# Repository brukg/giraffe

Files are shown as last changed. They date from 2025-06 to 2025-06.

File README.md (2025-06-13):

<!-- @format -->

# _giraffe: a low-cost robotic manipulator_ 🦒

```text
                                   __             ___  ___
                            .-----|__.----.---.-.'  _.'  _.-----.
                            |  _  |  |   _|  _  |   _|   _|  -__|
                            |___  |__|__| |___._|__| |__| |_____|
                            |_____|

                               Why should fun be out of reach?
```

A [Koch v1.1](https://github.com/jess-moss/koch-v1-1) inspired even more cost-effective, ROS2-compatible, Open-Source robotic manipulator designed to lower the barriers of entry for Embodied AI and whatever else your robotic dreams may be.

To achieve these outcomes, we implemented the following significant changes:

For changes/features in the previous version of the Giraffe, see [Giraffe v1.0](https://github.com/carpit680/giraffe/tree/v1.0?tab=readme-ov-file#design-enhancements).

<!-- START ANNOUNCEMENT -->
<section align="center">

## 🚀 OpenBot Community Launch! 🚀

🌐 **[Visit our Website](https://openbot.co.in)**  
📚 **[Read the Docs](https://docs.openbot.co.in)**  
💬 **[Join us on Discord](https://openbot.co.in/discord)**  
🛒 **[Get the Giraffe v1.1 Leader-Follower Set](https://www.openbot.co.in/#contact)**

Build along with the community, follow our progress, and get your hands on the very latest OpenBot hardware!

</section>
<!-- END ANNOUNCEMENT -->

## **Design Enhancements**

- Adjusted overall design for strength and ease of printing with minimal post processing requirement.
- Removable clamp base and Open Robotics Platform (ORP) mount for easy attachment to various robots.
- Designed a new Leader arm around the AS5600 12-bit magnetic encoder, which provides the same resolution at about 1/10 the price of any other Leader arm available.
- We have also designed a simple two layer PCB to replace the servo driver for Leader arm, there is always the option to build your own by hand on perf board. Schematics and Gerber files are available in the `/CAD/PCB/` directory.
- The Leader arm now uses a Wemos D1 Mini v2 or any other ESP8266/32 based microcontroller and can potentially teleoperate wirelessly.

- **[Teleop Tongs](https://github.com/carpit680/teleop_tongs) Integration**

  We integrated support for Teleop Tongs, another open-source project we built on top of [Dex Teleop](https://github.com/hello-robot/stretch_dex_teleop) (for the [Stretch 3](https://hello-robot.com/stretch-3-product) mobile manipulator by [Hello Robot](https://hello-robot.com/)), designed for teleoperating general-purpose robotic manipulators. This system features a 3D-printed tongs assembly equipped with multiple fiducial markers, serving as a stand-in for the end effector. This design enables intuitive and accessible control of the robotic arm.

  The motivation behind this integration was to offer a cost-effective, and user-friendly alternative to a leader & follower arm setup. By using Teleop Tongs, operators can manipulate the robotic arm naturally, simplifying teleoperation for applications in education, research, or DIY robotics projects.

---

## Assembly Instructions

| Giraffe Follower | Giraffe Leader |
|---|---|
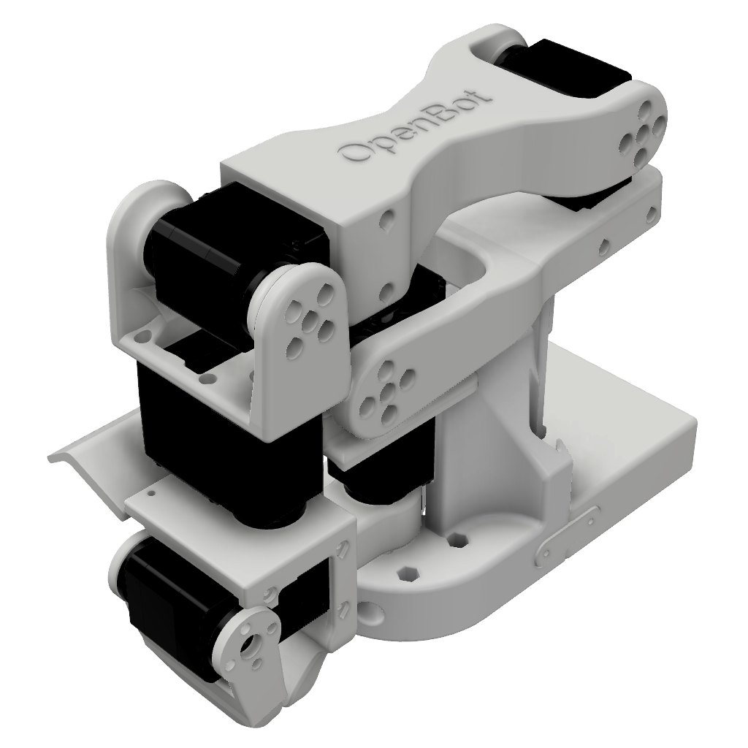
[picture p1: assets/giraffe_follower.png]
Giraffe Follower
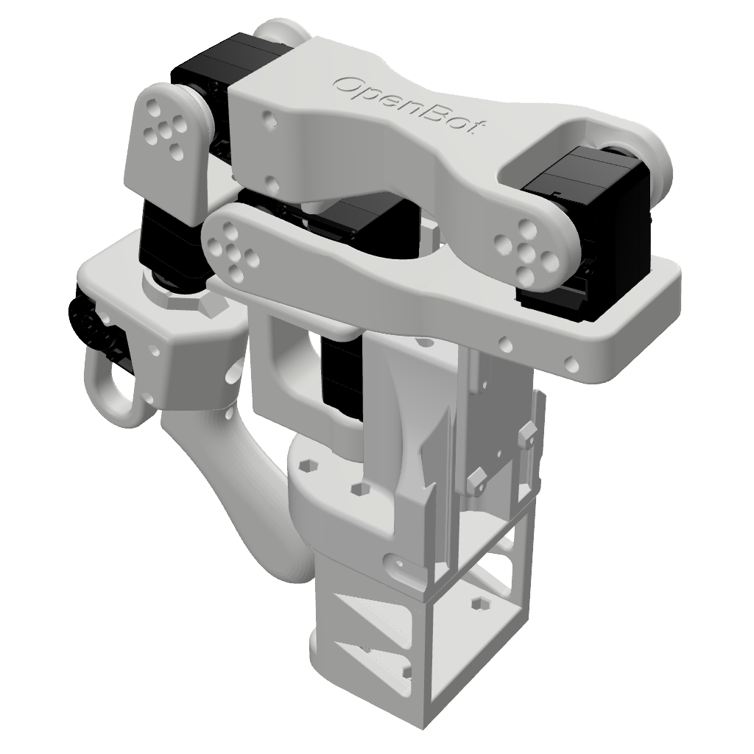
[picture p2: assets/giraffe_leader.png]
Giraffe Leader
|  |  |

> NOTE: We use a different(Servo 2) AS5600 servo casings for the wrist 2 and the gripper finger joint in the Leader arm. This is optional but recommended for more stable readings.

| Leader AS5600 encoder 1 | Leader AS5600 encoder 2 |
|---|---|
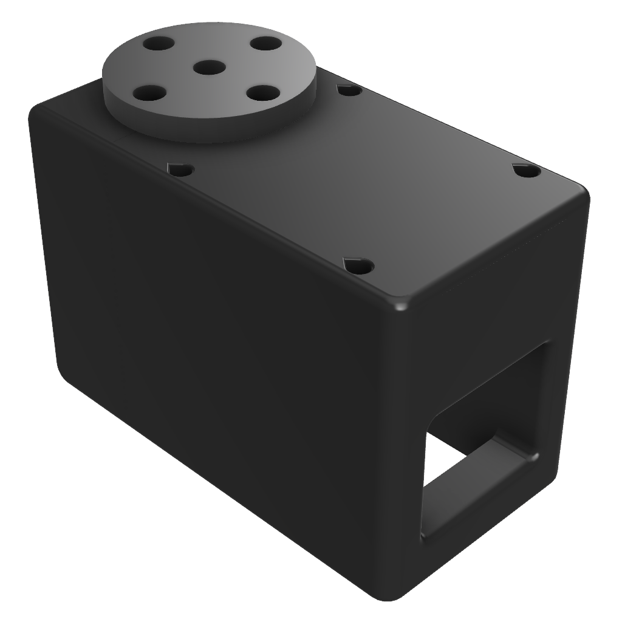
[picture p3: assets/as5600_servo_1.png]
Leader AS5600 servo 1
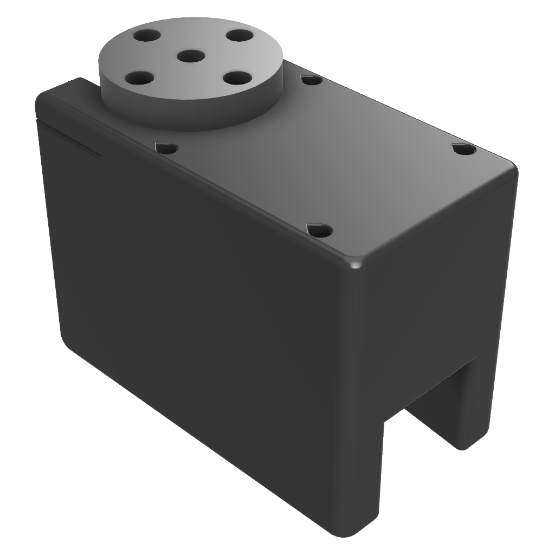
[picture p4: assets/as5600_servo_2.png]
Leader AS5600 servo 2
|  |  |

### Sourcing Parts

Order these off the shelf parts for the Leader and Follower arms using the Bill of Materials (BOM) below.

#### Follower Arm BOM

| Item Name | Quantity Per Arm | Unit Cost (incl GST) | Buy (India) |
| --- | --- | --- | --- |
| Waveshare 30KG Serial Bus Servo | 6 | ₹1,949.99 | [Think Robotics](https://thinkrobotics.com/products/30kg-serial-bus-servo-high-precision-and-torque-with-encoder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¤cy=INR&utm_medium=product_sync&utm_source=google&utm_content=sag_organic&utm_campaign=sag_organic&utm_source=googleads&utm_medium=cpc&gad_source=1&gad_campaignid=18347254777&gclid=Cj0KCQjw0qTCBhCmARIsAAj8C4ZDflwdPUv_pBn_uVcO5QZiu6YQNuyX5HaoNUr8UGUoSLmTD4PTMfQaApOWEALw_wcB) |
| Serial Bus Servo Driver Board | 1 | ₹508.86 | [Sharvi Electronics](https://sharvielectronics.com/product/serial-bus-servo-driver-board-integrates-servo-power-supply-and-control-circuit-applicable-for-st-sc-series-serial-bus-servos-w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) |
| 2 Inch metal C clamp  | 1 | ₹269.00 | [Amazon.in](https://www.amazon.in/Eastman-E-2036-C-CLAMP-INCH-2036/dp/B09F9F1KTF?th=1) |
| Type C USB Cable (1 metre) | 1 | ₹54.00 | [Robocraze](https://robocraze.com/products/type-c-usb-cable-1-metre?variant=40193636303001&country=IN¤cy=INR&utm_medium=product_sync&utm_source=google&utm_content=sag_organic&utm_campaign=sag_organic&campaignid=21590308288&adgroupid=&keyword=&device=c&gad_source=1&gclid=Cj0KCQjwqIm_BhDnARIsAKBYcmuNnQNnYDXqS_BIkwa01enR4i1DLvQ--OMAT0BC9CL8HVrOcXE4uf0aAkGMEALw_wcB) |
| 12V 5A 60W Power Supply with 5.5mm DC Plug | 1 | ₹403.00 | [Robu.in](https://robu.in/product/orange-ac-100-240v-to-dc-12v-5a-60w-power-adapter/) |
| Total | --- | ₹12,935 | --- |

#### Leader Arm BOM

| Item Name | Quantity Per Arm | Unit Cost (incl GST) | Buy (India) |
| --- | --- | --- | --- |
| 30 AWG wire 1m | 5 | ₹5.00 | [Robu.in](https://robu.in/product/high-quality-ultra-flexible-30awg-silicone-wire-1000-m-white/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) |
| Perf Board | 0.25 | ₹142.00 | [Robu.in](https://robu.in/product/12-x-18-cm-universal-pcb-prototype-board-single-sided-2-54mm-hole-pitch/) |
| Wemos D1 mini v2 | 1 | ₹182.00 | [Robu.in](https://robu.in/product/d1-mini-v2-nodemcu-4m-bytes-lua-wifi-internet-of-things-development-board-based-esp8266/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) |
| TCA9548A I2C Mux | 1 | ₹81.21 | [Zbotic](https://zbotic.in/product/cjmcu-tca9548a-i2c-8-channel-multiple-extensions-development-board/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) |
| AS5600 Encoder | 6 | ₹130.80 | [Quartz Components](https://quartzcomponents.com/products/as5600-magnetic-angle-encoder-sensor-module?variant=44904504492266) |
| M3 x 6 philips head bolts | 48 | ₹3.00 | [Only Screws](https://onlyscrews.in/products/hex-allen-socket-head-m3-x-6-screw-pack-of-20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) |
| M2.2 x 9.5 philips head self tapping screws | 2 | ₹47.20 | [Robotics DNA](https://roboticsdna.in/product/2-2mm-dia-9-5mm-ss-self-tapping-screw-25-pieces/?src=google&kwd=&adgroup={adgroup}&device=c&campaign={campaign}&adgroup={adgroup}&keyword=&matchtype=&gad_source=1&gad_campaignid=22411741198&gclid=Cj0KCQjw0qTCBhCmARIsAAj8C4YcSURfn4xIPfqC6ZU851A3e9wjm49ESc_jJkYKZkwkTw2ZjKHKA_AaAkHNEALw_wcB) |
| Micro USB B cable 1 metre | 1 | ₹35.00 | [Robocraze](https://robocraze.com/products/usb-to-micro-usb-cable?variant=40192442007705&country=IN¤cy=INR&utm_medium=product_sync&utm_source=google&utm_content=sag_organic&utm_campaign=sag_organic&utm_source=google&utm_medium=cpc&utm_campaign=BL+%7C+Pmax+%7C+Feed+Only+%7C+Top+40+Revenue+%7C+09%2F06&utm_source=googleads&utm_medium=ppc&utm_campaign=21373062889&utm_content=_&utm_term=&campaignid=21373062889&adgroupid=&campaign=21373062889&gad_source=1&gclid=Cj0KCQjw2N2_BhCAARIsAK4pEkVDPtNGpsZV-ffHMIzdULpzGFAPsKl39PljBhO8jgnAKcCk_V_ssa4aAiHVEALw_wcB) |
| 2 Inch metal C clamp  | 1 | ₹269.00 | [Amazon.in](https://www.amazon.in/Eastman-E-2036-C-CLAMP-INCH-2036/dp/B09F9F1KTF?th=1) |
| Total | --- | ₹1,651 | --- |

### Printing The Parts

A variety of 3D printers can be used to print the necessary parts for the arm. Follow these steps for optimal printing results.

#### 1. Select A Printer

When choosing a printer, keep the following recommended specifications in mind. While other printers may work, these specifications are a good starting point:

- **Layer Height:** Minimum 0.2mm
- **Material:** PLA+, ABS, PETG, or other durable plastics
- **Nozzle Diameter:** Maximum 0.4mm
- **Infill Density:** Approximately 30%
- **Suggested Printers:** Prusa Mini+, Bambu P1, Ender3, and similar models

#### 2. Prepare The Printer

- **Materials Needed:**

  - Standard Glue Stick
  - Putty Knife

- **Setup and Printing Process:**
  1. Calibrate the printer and level the print bed following your printer’s specific instructions.
  2. Clean the print bed, removing any dust or grease. If you use water or other cleaning agents, ensure the bed is fully dry.
  3. Apply a thin, even layer of glue to the print area. Avoid uneven application or clumps.
  4. Load the printer filament according to the printer's guidelines.
  5. Adjust the printer settings to match the recommended specifications listed above.
  6. Verify the file format, select files from the hardware folder, and begin printing.

#### 3. Print The Parts

Print one of each part found in `/CAD/STL/common/` and `/CAD/STL/follower/` or `/CAD/STL/leader/` directories, depending on whether you are building the follower or leader arm. The files are organized as follows:

<div align="center">

| Common for Follower & Leader | Follower Arm Only | Leader Arm Only |
|:---|:---|:---|
| base | follower_base_retainer_left | as5600_servo_1 |
| servo_driver_mount | follower_base_retainer_right| as5600_servo_2 |
| shoulder_pan | follower_clamp_base | leader_clamp_base |
| shoulder_pan_retainer | follower_wrist_2 | leader_wrist_2 |
| shoulder_pan_pin | follower_gripper_finger | leader_handle |
| shoulder_lift | | leader_gripper_finger |
| elbow | | |
| wrist_1 | | |

</div>

#### 4. Take Down

- After the print is done, use the putty knife to scrape the the parts off the print bed.
- Remove any support material from parts.

### Assembling The Parts

Follow the assembly guide given in the [OpenBot Docs](https://docs.openbot.co.in/docs/Giraffe/giraffe_intro) to assemble the parts. The assembly process is similar for both the Leader and Follower arms, with some differences in the Leader arm due to the AS5600 encoders and the Wemos D1 Mini.

The assembled arms would look something like this:

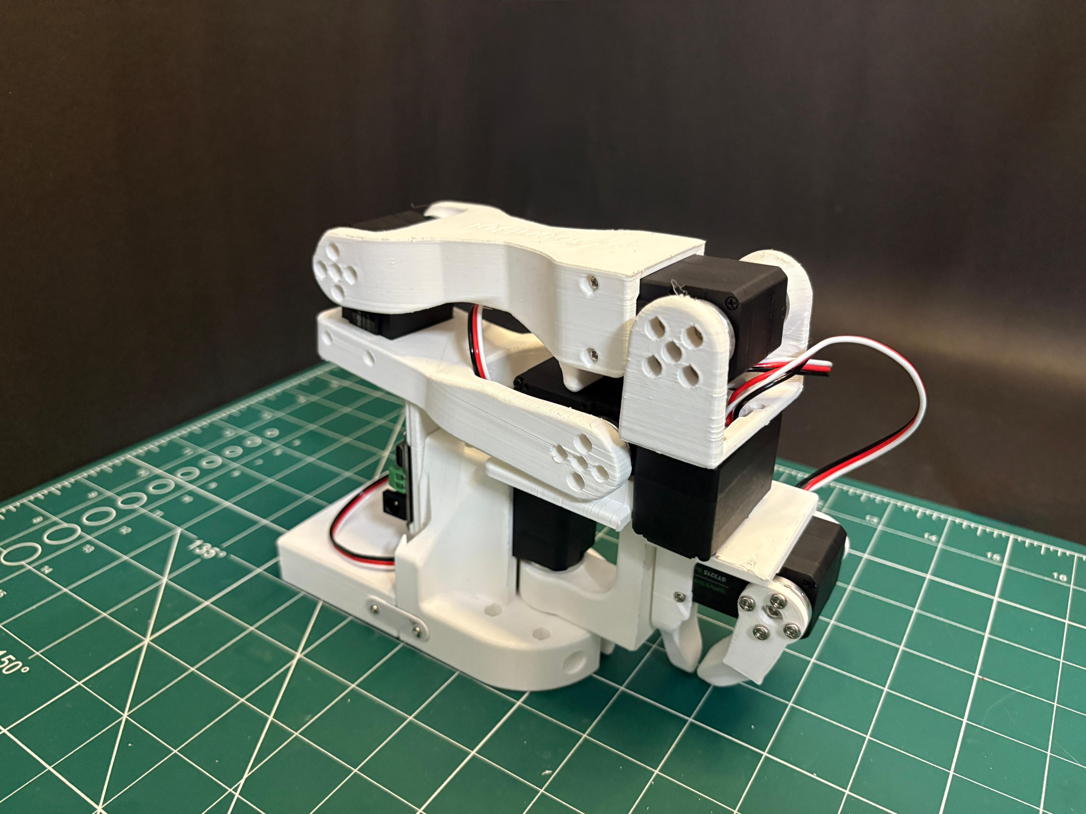
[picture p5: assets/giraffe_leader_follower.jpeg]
Image of Giraffe leader and follower arms


---

## Hardware Setup Instructions

> NOTE: Configurator and the rest of the high-level software stack is presently only compatible with Python.

### Clone The [giraffe](https://github.com/carpit680/giraffe) Repository

```bash
git clone https://github.com/carpit680/giraffe.git
cd giraffe
```

### Install Dependencies

```bash
pip install -r requirements.txt
pip install .
```

### Setup Permissions

```bash
sudo usermod -a -G dialout $USER
sudo newgrp dialout
```

### Setup Servo IDs

Use the configurator script in `scripts/` directory

```bash
python3 scripts/st_configurator.py
```

---

## Optional ROS2 Docker Development Environment Setup

Follow the instructions given here to set up a ROS2 Docker development environment: [ros2_docker_env](https://github.com/carpit680/ros2_docker_env)

## ROS2 Worksapce Setup

1. Install ROS2 Humble following these [installation instructions](https://docs.ros.org/en/humble/Installation.html).
2. Install Gazebo Ignition Fortress(LTS) following these [instructions](https://gazebosim.org/docs/fortress/install_ubuntu/).
3. Install Moveit 2

   ```bash
   # Install MoveIt 2 for ROS 2 Humble
   sudo apt update
   sudo apt install -y ros-humble-moveit
   ```

4. Install other dependencies

   ```bash
   sudo apt install -y ros-humble-ros2-control ros-humble-ros2-controllers
   sudo apt install -y python3-colcon-common-extensions python3-rosdep
   ```

5. Set Up giraffe_ws

   ```bash
   # Clone giraffe repository if you have not done so already

   # Update dependencies using rosdep
   cd <path-to-giraffe-repo>/giraffe_ws
   sudo rosdep init  # Only if not already initialized
   rosdep update
   rosdep install --from-paths src --ignore-src -r -y
   ```

6. Build and source the workspace

   ```bash
   cd <path-to-giraffe-repo>/giraffe_ws
   colcon build --symlink-install

   source install/local_setup.zsh
   # OR
   source install/local_setup.bash
   ```

## ROS2 Workspace Description
[moveit_demo.webm](https://github.com/user-attachments/assets/742ece26-183e-449f-bbf9-ddf3f7e3e628)

### giraffe_description

This package contains URDF for _giraffe_ robotic manipulator along with ros2 control xacro, ros2 controller config files, and the launch files for the entire workspace.

- _display.launch.py_: This launch file visualizes the giraffe robot model in ROS 2. It includes:

  1. Robot State Publisher: Publishes the robot's state using the URDF.
  2. Joint State Publisher GUI: Enables interactive joint control.
  3. RViz Visualization: Displays the robot in a pre-configured RViz environment.

  _Usage_:

  ```bash
  ros2 launch giraffe_description display.launch.py
  ```

- _simulation.launch.py_: This launch file sets up the simulation environment for the giraffe robot in Gazebo and RViz. It includes:

  1. Gazebo Simulation: Starts Gazebo server and client with the giraffe robot model.
  2. Robot Description and State Publisher: Publishes the robot's URDF and joint states.
  3. Controllers: Spawns and activates controllers for joint trajectory and gripper control.
  4. RViz Visualization: Displays the robot model and state in RViz.

  _Usage_:

  ```bash
  ros2 launch giraffe_description simulation.launch.py
  ```

- _moveit_sim.launch.py_: This launch file integrates the giraffe robot with Gazebo, MoveIt! 2, and RViz for advanced motion planning and control. Key features:

  1. Gazebo Integration:
      - Spawns the giraffe robot in Gazebo.
      - Configures ros2_control and joint controllers.
  2. MoveIt! 2 Motion Planning:
      - Loads MoveIt! 2 configurations (SRDF, kinematics, OMPL planning).
      - Starts the move_group node for motion planning and execution.
  3. RViz Visualization:
      - Launches RViz preconfigured for MoveIt! 2 to visualize and interact with the robot.

  _Usage_:

  ```bash
  ros2 launch giraffe_description moveit_sim.launch.py
  ```

- moveit_interface.launch.py_: This launch file configures and launches the giraffe robot hardware, MoveIt! 2, and a hardware interface for motion control. Key features:

  1. MoveIt! 2 Motion Planning:
      - Loads MoveIt! 2 configurations (SRDF, kinematics, and OMPL planning).
      - Starts the move_group node for motion planning and trajectory execution.
  2. RViz Visualization:
      - Displays the robot's state and motion planning visualization using a preconfigured RViz setup.
  3. Hardware Interface:
      - Includes a node for the giraffe robot's hardware interface for integration with controllers.

  _Usage_:

  ```bash
  ros2 launch giraffe_description moveit_interface.launch.py
  ```

### giraffe_moveit_config

The giraffe_moveit_config package provides the MoveIt! 2 configuration for the 5-DoF robotic arm named "Giraffe," designed for use with ROS 2 Humble. It includes essential files for motion planning and execution, such as:

- **URDF and SRDF**: Defines the robot's kinematic structure and semantic description.
- **Kinematics Configuration**: Specifies IK solvers for planning.
- **OMPL Planning Configuration**: Configures planning pipelines for trajectory generation.
- **Controller Configuration**: Integrates with ros2_control for real-time trajectory execution.
- **RViz Configuration**: Pre-configured visualization setup for MoveIt! 2.

This package is utilized by the **giraffe_description** package's launch file to enable simulation and motion planning for the Giraffe arm in Gazebo and MoveIt! 2 environments.

### giraffe_control
The giraffe_control package provides hardware-level control for the 5-DoF Giraffe robotic arm. It includes a ROS 2 node, giraffe_driver, and a corresponding launch file to facilitate communication between ROS 2 and the physical hardware.

#### Features

1. Giraffe Servo Driver (giraffe_driver):

   - Implements direct communication with the Giraffe arm's servos using the Feetech motor bus.
   - Processes incoming command messages to set motor positions.
   - Read motor position feedback from the servos to publish feedback.
   - Supports homing offsets, acceleration settings, and position conversion from radians to motor steps.
   - Subscribes to /command for joint commands and publishes feedback to /feedback topic.
   - Interfaces with six motors:
     - base_link_shoulder_pan_joint
     - shoulder_pan_shoulder_lift_joint
     - shoulder_lift_elbow_joint
     - elbow_wrist_1_joint
     - wrist_1_wrist_2_joint
     - wrist_2_gripper_joint

2. Launch File:
   - Starts the giraffe_driver node.
   - Configures parameters for easy integration with other ROS 2 packages.

_Usage_:

The giraffe_control package is used by the giraffe_description package's launch file to provide hardware control during simulations and real-world operation. It ensures seamless integration of the Giraffe robotic arm into ROS 2 for both motion execution and feedback.

### giraffe_hardware
The giraffe_hardware package provides a ros2_control hardware interface for the Giraffe 5-DoF robotic arm plus a gripper joint. This interface lets you control and monitor the arm through standard ROS 2 controllers and topics, simplifying integration with motion planning frameworks like MoveIt.

#### Features:

1. Giraffe Hardware Interface (GiraffeInterface):
   - Implements a hardware_interface::SystemInterface plugin.
   - Subscribes to feedback (sensor_msgs/msg/JointState) for joint position updates.
   - Publishes to command (sensor_msgs/msg/JointState) to send joint commands.
   - Handles all six joints of the arm.

_Usage_:

- Integrate with controller_manager and standard controllers (e.g., joint_trajectory_controller).
- Place giraffe_interface in your ros2_control configuration.
- Commands and feedback are exchanged via standard ROS topics, enabling easy simulation or real hardware operation.

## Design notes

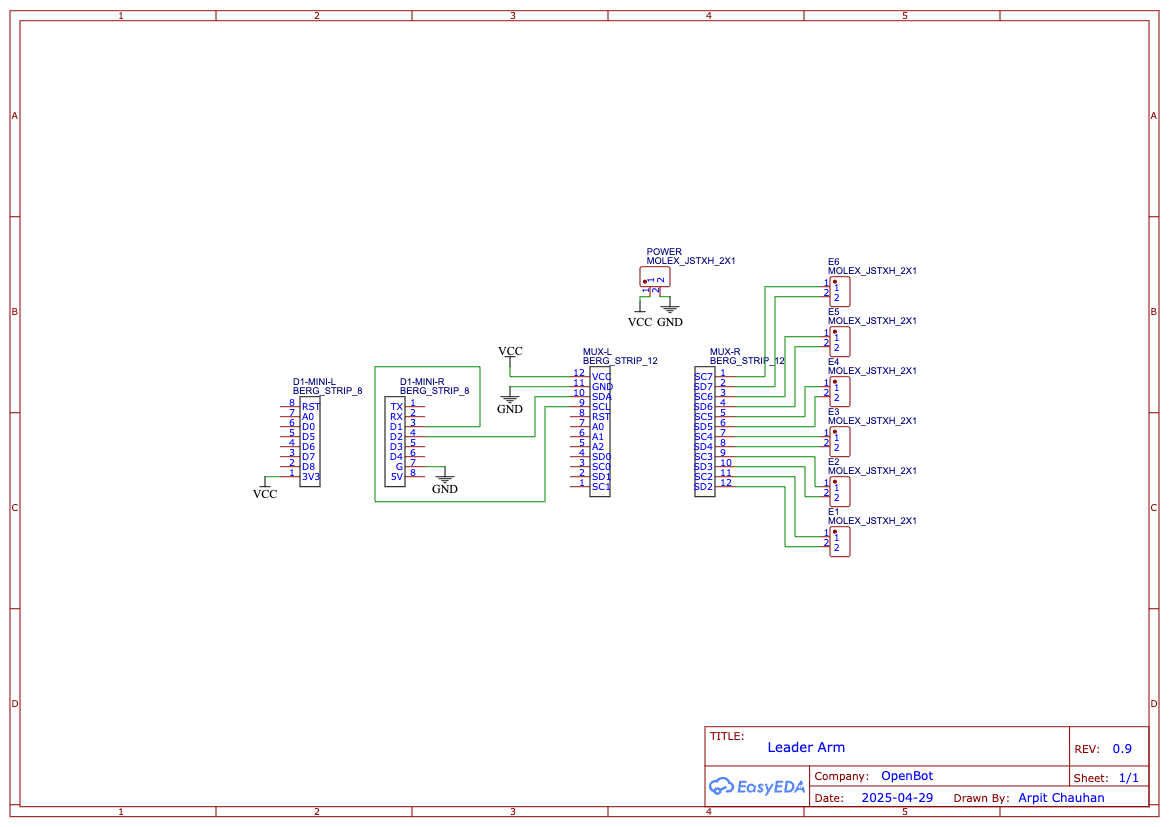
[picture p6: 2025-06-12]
CAD/PCB/Schematic_OpenBot-Leader-Arm-v0.9_2025-06-12.png

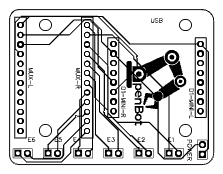
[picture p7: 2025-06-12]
CAD/PCB/PCB_PCB_OpenBot-Leader-Arm-v0.9_2025-06-12.png

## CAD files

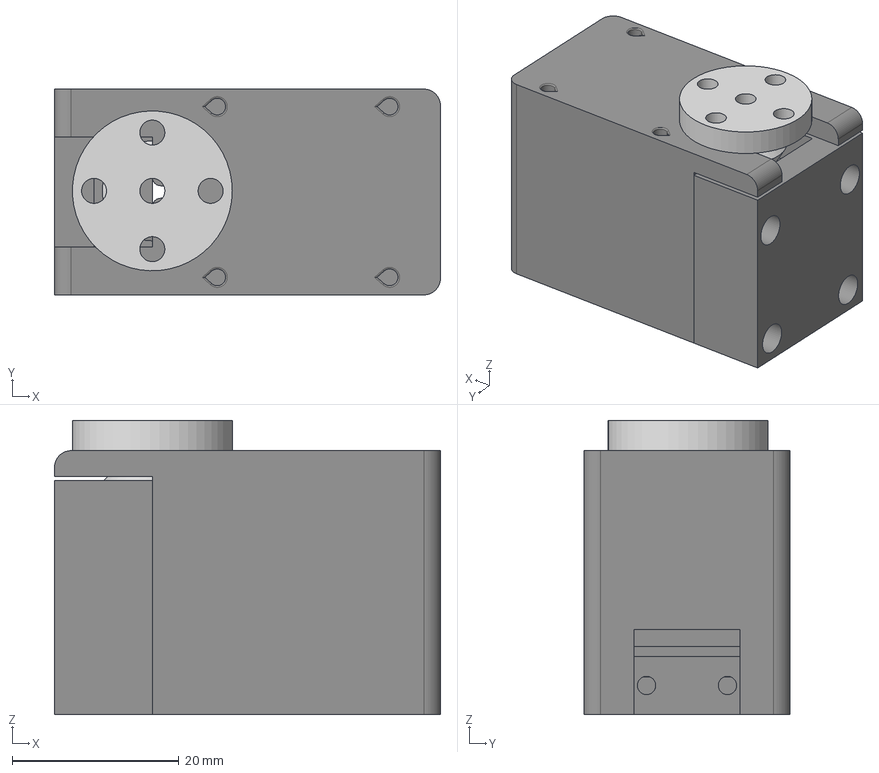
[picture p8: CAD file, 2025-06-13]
CAD/STEP/as5600_servo_2.step
46.4 x 24.7 x 35.3 mm
AS5600_Base
AS5600_Shaft_Holder v4
AS5600_Shaft v3
retainer

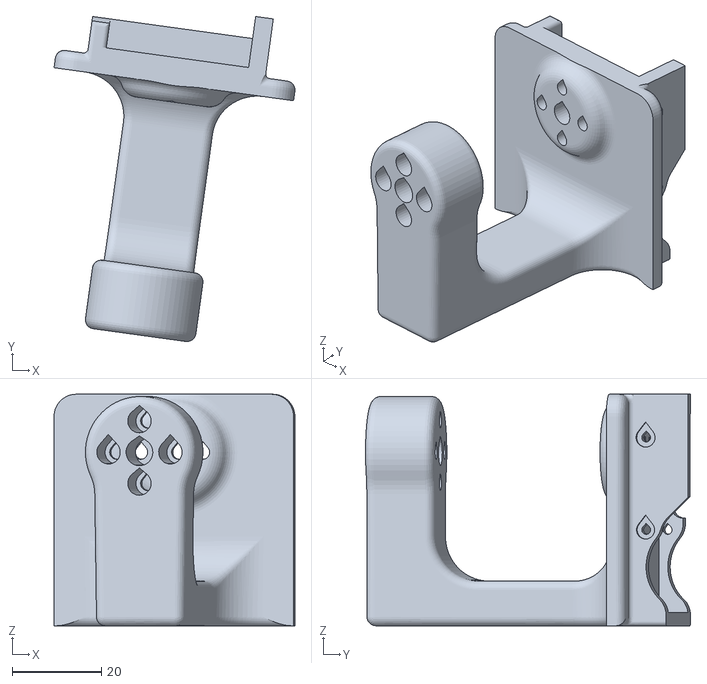
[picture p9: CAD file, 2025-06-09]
CAD/STL/common/shoulder_pan.stl
54.0 x 72.8 x 51.9

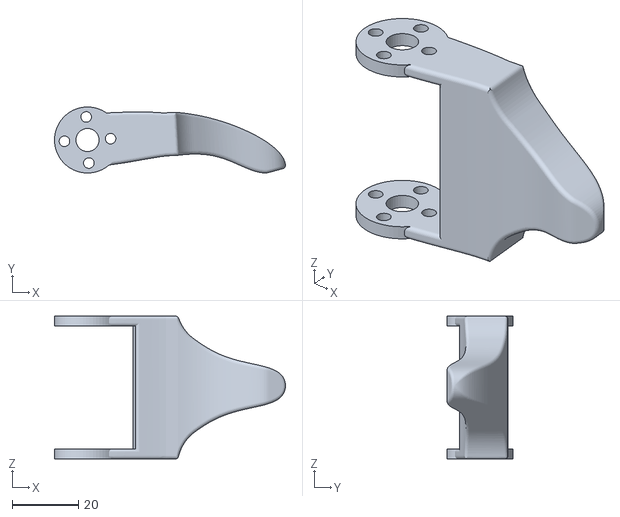
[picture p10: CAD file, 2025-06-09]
CAD/STL/follower/follower_gripper_finger.stl
69.9 x 20.0 x 43.2

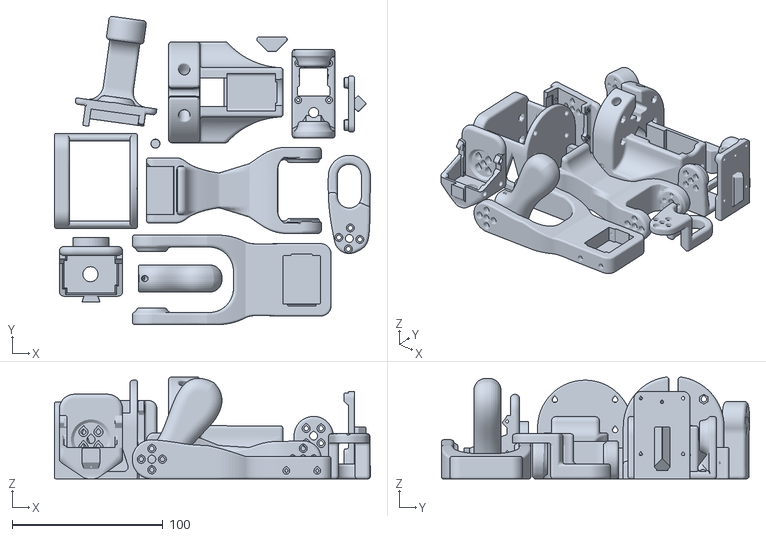
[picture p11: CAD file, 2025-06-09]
CAD/STL/Giraffe Leader v1.1.stl
209.5 x 204.4 x 67.6

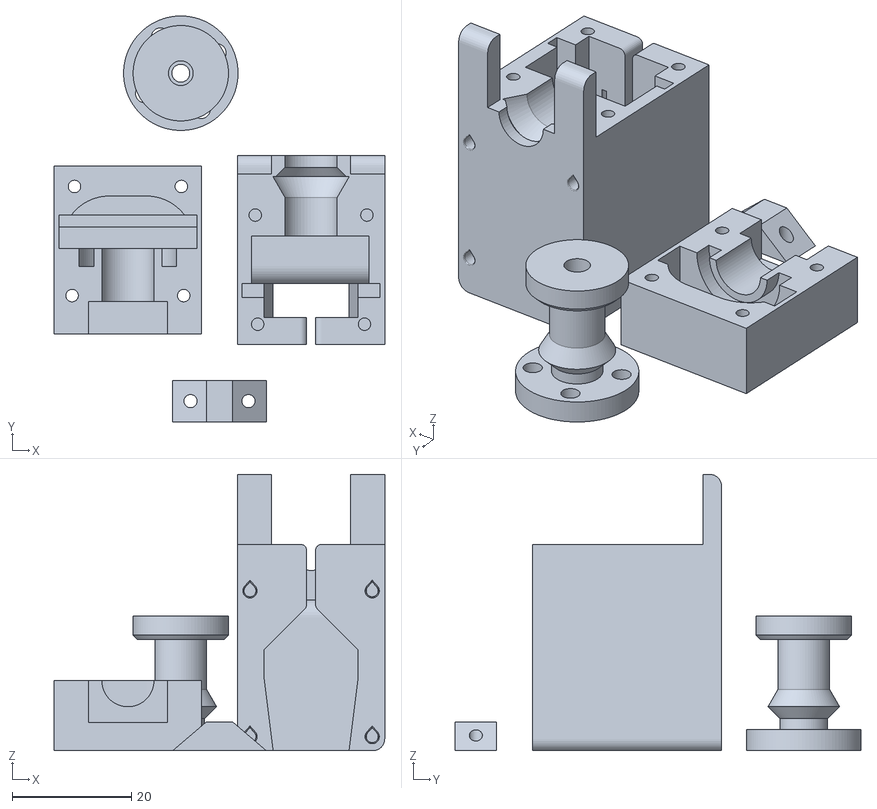
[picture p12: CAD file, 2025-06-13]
CAD/STL/leader/as5600_servo_2.stl
55.4 x 68.1 x 46.4

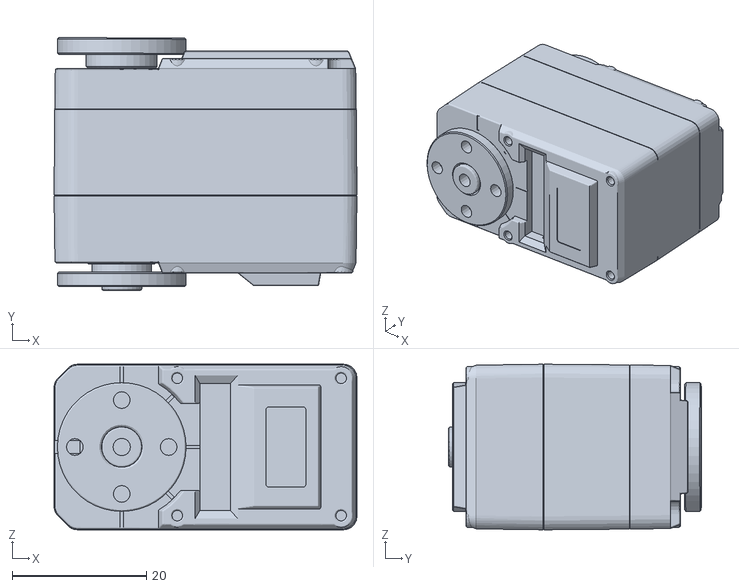
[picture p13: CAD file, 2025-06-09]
giraffe_ws/src/giraffe_description/meshes/wrist_1_actuator.stl
45.2 x 37.7 x 24.7

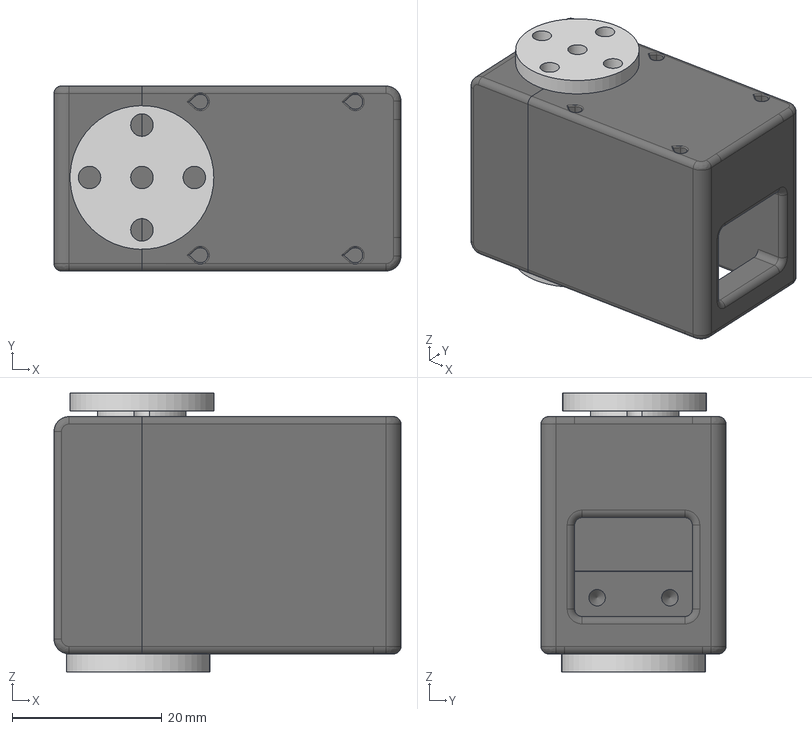
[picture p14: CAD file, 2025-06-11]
CAD/STEP/as5600_servo_1.step
46.4 x 24.7 x 37.2 mm
AS5600_Base
AS5600_Sensor
AS5600_Shaft_Holder v4
AS5600_Shaft v3
AS5600_Cap v2
cable_retainer

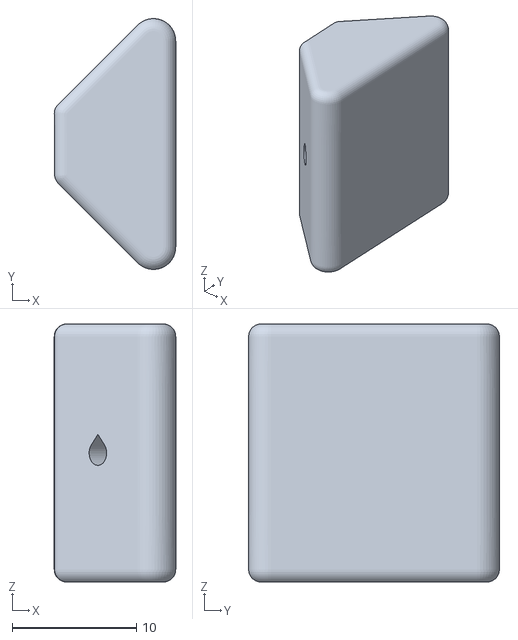
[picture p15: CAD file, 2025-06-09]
CAD/STL/common/shoulder_pan_retainer.stl
9.80 x 20.2 x 20.8

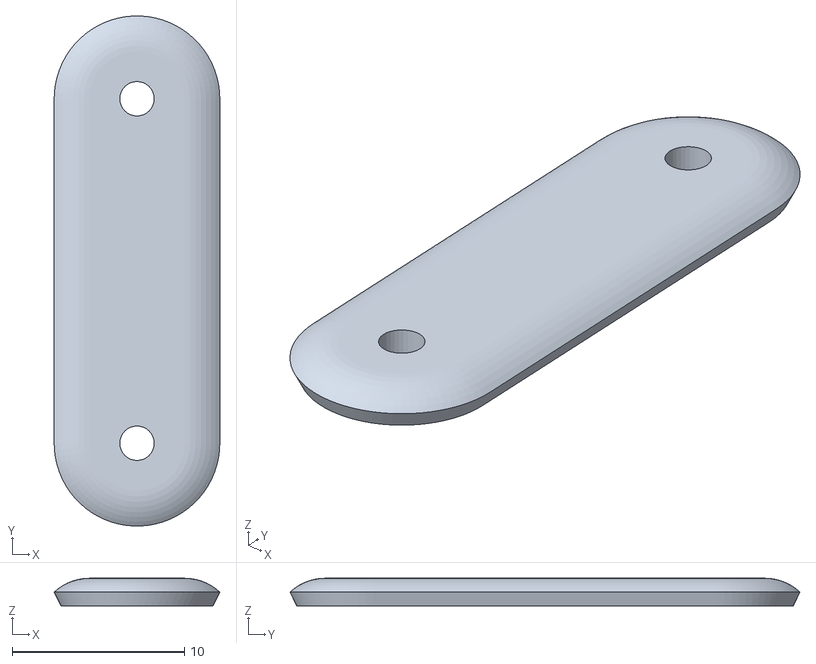
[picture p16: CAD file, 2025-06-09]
CAD/STL/follower/follower_base_retainer_right.stl
9.62 x 29.6 x 1.60

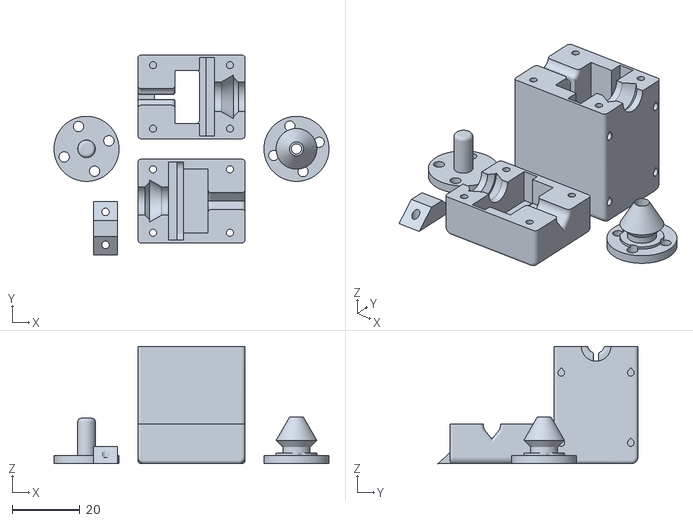
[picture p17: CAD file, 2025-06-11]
CAD/STL/leader/as5600_servo_1.stl
81.1 x 59.0 x 34.6

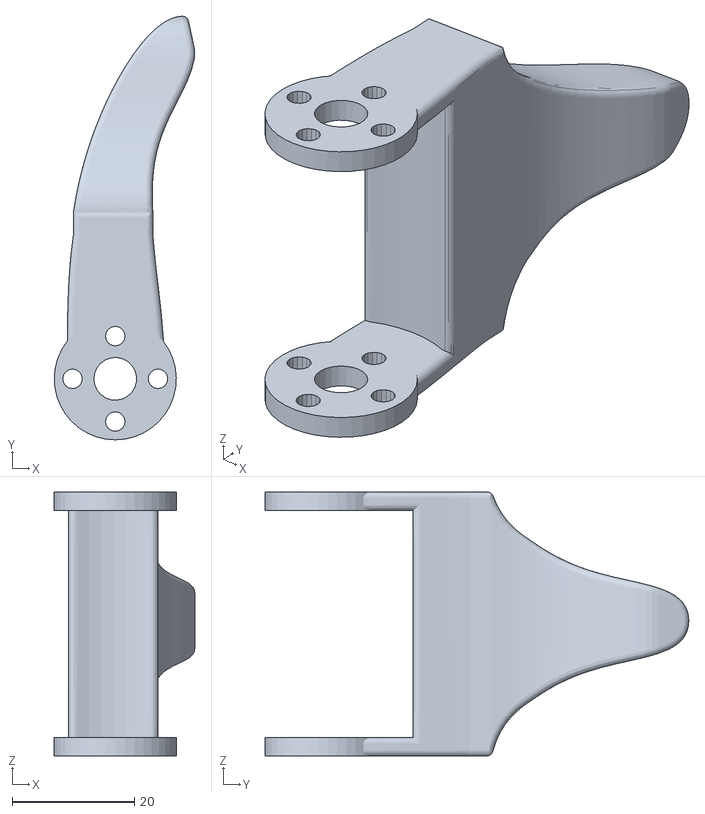
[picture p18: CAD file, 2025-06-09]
giraffe_ws/src/giraffe_description/meshes/gripper.stl
23.0 x 69.4 x 43.3

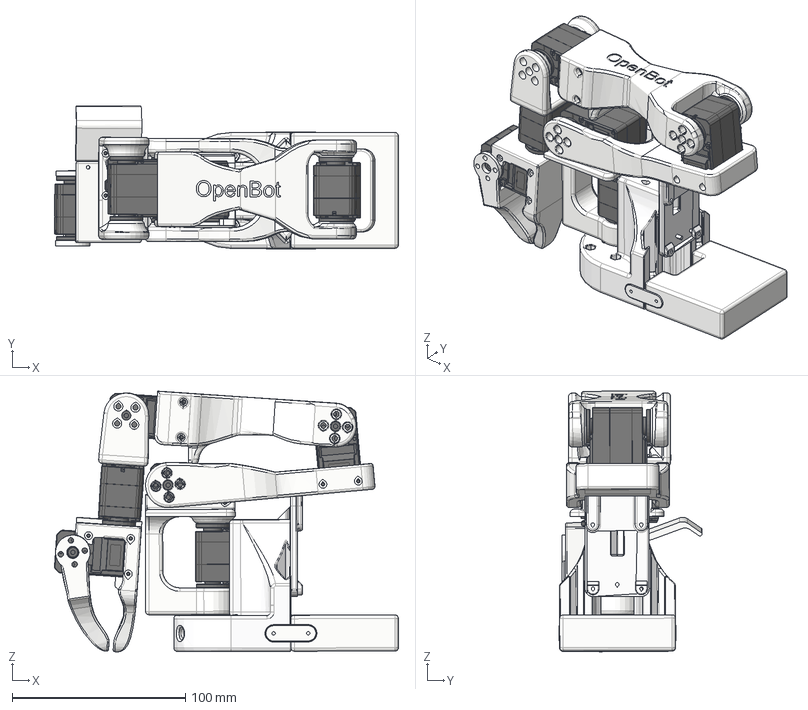
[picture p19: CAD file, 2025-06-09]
CAD/STEP/Giraffe v1.1.step
198.7 x 82.7 x 150.6 mm
shoulder_pan_shaft
Follower_Gripper_Static_Part
shoulder_pan
SCS215_1
servo_driver_mount
base_link_1
clamp_base
retainer
base_brace
base_brace1
shoulder_lift
elbow_link
wrist1_link
Follower_Gripper_Moving_Part
camera_mount
SCS215_1_1
SCS215_1_2
SCS215_1_3
SCS215_1_4
SCS215_1_5

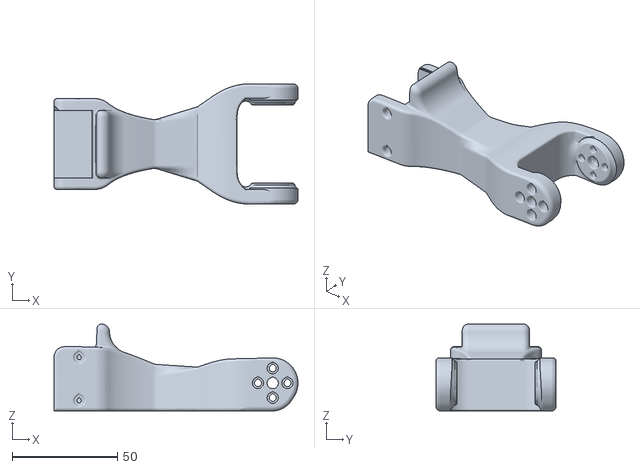
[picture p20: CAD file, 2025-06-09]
CAD/STL/common/elbow.stl
115.9 x 57.2 x 41.3

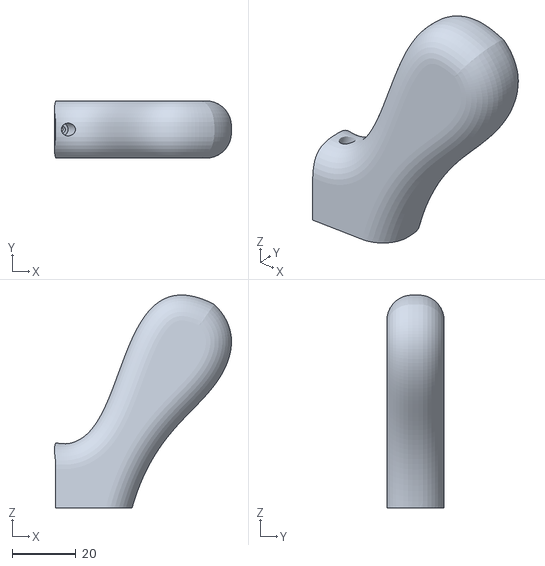
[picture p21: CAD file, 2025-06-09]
CAD/STL/leader/leader_handle.STL
55.5 x 18.0 x 66.7

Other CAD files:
CAD/STL/follower/follower_base_retainer_left.stl
giraffe_ws/src/giraffe_description/meshes/shoulder_lift.stl
CAD/STL/common/shoulder_lift.stl
CAD/STL/follower/follower_wrist_2.stl
CAD/MuJoCo/giraffe/meshes/base_brace_left.stl
CAD/MuJoCo/giraffe/meshes/base_brace_right.stl
CAD/MuJoCo/giraffe/meshes/base_link.stl
CAD/MuJoCo/giraffe/meshes/camera_mount.stl
CAD/MuJoCo/giraffe/meshes/clamp_base.stl
CAD/MuJoCo/giraffe/meshes/elbow_actuator.stl
CAD/MuJoCo/giraffe/meshes/elbow_link.stl
CAD/MuJoCo/giraffe/meshes/finger_actuator.stl
CAD/MuJoCo/giraffe/meshes/gripper.stl
CAD/MuJoCo/giraffe/meshes/retainer.stl
CAD/MuJoCo/giraffe/meshes/servo_driver_mount.stl
CAD/MuJoCo/giraffe/meshes/shoulder_lift.stl
CAD/MuJoCo/giraffe/meshes/shoulder_lift_actuator.stl
CAD/MuJoCo/giraffe/meshes/shoulder_pan.stl
CAD/MuJoCo/giraffe/meshes/shoulder_pan_actuator.stl
CAD/MuJoCo/giraffe/meshes/shoulder_pan_shaft.stl
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

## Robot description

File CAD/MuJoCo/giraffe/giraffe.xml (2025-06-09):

<mujoco model="giraffe">
    <compiler angle="radian" />
    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
    <worldbody>
        <light directional="true" pos="-0.5 0.5 3" dir="0 0 -1" />
        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
        <body name="base_link" pos="0.0091690160088054 -0.02359412617182375 0.010942348559247783" euler="0.0024434609528024677 -0.0024434609527765054 1.5715549810200333">
            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
            <inertial mass="0.7829139108662936" pos="-1.412344777073935e-06 -0.01167323000933829 0.014490543974002491" fullinertia="0.000590727637349527 0.0006369098056043479 0.0005080336997379469 -9.27362070721634e-09 5.490385866527081e-08 0.00013734127707619903" />
            <body name="base_brace_left" pos="0.00219848269213204 2.4115243135724997e-12 -0.010999999993761798" euler="2.3187674740368642e-10 3.7296554733501343e-16 -0.0007586542251338164">
                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
                <inertial mass="0.0028935307422124647" pos="-0.035253910718120875 -0.036931608191481315 0.010400000022961495" fullinertia="1.9353041846348793e-07 1.890869415337324e-08 1.7575661258467082e-07 1.3249345900948496e-10 -4.484263291773439e-15 -5.153167221012219e-15" />
                <body name="clamp_base" pos="-0.0051940438279875776 -0.0058529421672603565 4.193728697643451e-14" euler="7.159763233677289e-13 4.510281037539701e-17 -1.1676942100963608e-16">
                    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
                    <inertial mass="0.635930553849011" pos="0.0030488003636385307 -0.06350547271076666 0.010450675413364285" fullinertia="0.0002171618148138281 0.00027238210225702327 0.0004441779848429455 -5.441750870557369e-08 6.923158179202346e-10 -1.147371898099061e-06" />
                </body>
            </body>
            <body name="base_brace_right" pos="-0.0022000000000001086 2.422179123939827e-12 -0.010999999993733188" euler="2.3291047562823413e-10 -3.816391647148976e-17 -0.0007586542251338723">
                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
                <inertial mass="0.0028935307298555263" pos="0.03530990667221308 -0.03687807450437343 0.010400000010492332" fullinertia="1.9353042647958055e-07 1.8908702793434855e-08 1.757566288606501e-07 1.324706261934331e-10 1.9741289582480517e-15 -2.257223133111565e-15" />
            </body>
            <body name="servo_driver_mount" pos="-1.1035616864774056e-13 0.00886674779218549 0.010000000000003633" euler="7.871567980766161e-14 -1.2273168592535915e-16 2.3103980056562606e-12">
                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
                <inertial mass="0.08394897351119068" pos="-0.00014447256054325508 -0.047460538463202875 0.0414553116305895" fullinertia="2.299788286622743e-05 3.1489571620153476e-05 9.399130628228765e-06 -1.1204368278905487e-08 -3.5409012661794584e-10 -6.713156318615722e-08" />
            </body>
            <body name="retainer" pos="0.0 -1.0547118733938988e-16 -0.0055000000000000005" euler="-1.5872719805187787e-16 -1.7217130499069815e-16 -0.0007586542251338728">
                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
                <inertial mass="0.023167704459451238" pos="-1.0982526000321547e-05 0.015182539103881183 0.004899368620599504" fullinertia="9.855699104456957e-07 1.3643893497675718e-06 6.898950720422228e-07 -5.261763725870215e-10 -7.929944952334602e-14 1.7467517866131746e-11" />
            </body>
            <body name="shoulder_pan_actuator" pos="-7.397177513217556e-06 -0.017444148046101775 0.05334999999999862" euler="-1.5707963267948963 -1.5707963267948963 0">
                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
                <inertial mass="0.05588569179115004" pos="-0.013154933044561045 -0.009175814107191095 -1.8105566209090373e-07" fullinertia="7.510362600149057e-06 1.2037413533205136e-05 1.4109760903697583e-05 -6.650557424937638e-08 -5.272657727276987e-10 4.839065848300531e-10" />
                <body name="shoulder_pan" pos="-0.017444155976299138 -0.06434999999999907 -1.3508780905984174e-05" euler="-1.570796326795054 -8.776399745835646e-15 1.5707963267949236">
                    <joint name="shoulder_pan_actuator_shoulder_pan_joint" type="hinge" axis="-4.508054795705589e-07 4.5878730598348377e-07 -0.9999999682667913" pos="-1.312613493342039e-05 0.008056244052512191 0.036699521993512105" />
                    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
                    <inertial mass="0.3368588301981278" pos="0.0002542459584769539 0.02623097408147771 0.05867499174414719" fullinertia="0.00027438094637329495 0.00023295755518516658 0.00012072319168036025 1.6462641073505106e-06 -2.9920786751209986e-06 6.162337830722745e-06" />
                    <body name="shoulder_pan_shaft" pos="8.628653347386717e-15 -4.440892098500626e-16 0.0005499999999999247" euler="-0.0 4.336808689942018e-19 1.3891340334970523e-19">
                        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
                        <inertial mass="0.0042142577056196355" pos="-1.3508781529601174e-05 0.008055844023700841 0.02613973216489793" fullinertia="1.5084783731102806e-07 1.5084783503213017e-07 1.764573803493461e-08 7.710201784498272e-22 2.6932313150842396e-19 -2.5285877349980365e-21" />
                    </body>
                    <body name="shoulder_lift_actuator" pos="0.009636491219081512 0.00826308092216846 0.09612607413828171" euler="-6.20163642661711e-17 -3.3393426912553666e-17 -1.5707963267948966">
                        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
                        <inertial mass="0.05588569179115005" pos="-0.013154933044560885 -0.00917581410719114 -1.8105566208872516e-07" fullinertia="7.510362600148801e-06 1.2037413533205544e-05 1.4109760903697226e-05 -6.650557424938906e-08 -5.272657727008104e-10 4.839065848630642e-10" />
                        <body name="shoulder_lift" pos="-0.08067218938120414 -0.009029067312597632 0.01299462027768497" euler="-3.141590799844319 -2.6020852139651964e-18 -1.5683528665452828">
                            <joint name="shoulder_lift_actuator_shoulder_lift_joint" type="hinge" axis="1.0000004184208011 2.025841990926285e-07 4.270431128174622e-07" pos="0.018661792414646203 0.05513022762674431 0.01299975031070518" />
                            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
                            <inertial mass="0.48698957738534054" pos="1.88345976199684e-05 -0.0023027278513623405 0.008938984574311698" fullinertia="0.0006143127393543786 0.00020406932575313223 0.0007846240648212774 -2.3438943887091353e-07 6.898050884627582e-08 -3.843703366668296e-05" />
                            <body name="elbow_actuator" pos="0.009602583188114229 -0.04429567734851477 0.012670109989027446" euler="1.5707963267948968 2.6427427954334257e-19 -1.570796326794897">
                                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
                                <inertial mass="0.05588569179115005" pos="-0.013154933044560857 -0.009175814107191139 -1.8105566209709385e-07" fullinertia="7.510362600148832e-06 1.2037413533205453e-05 1.4109760903697395e-05 -6.650557424935312e-08 -5.272657727686988e-10 4.839065848357534e-10" />
                                <body name="elbow_link" pos="-0.03383746211262231 -0.01941177480014052 -0.07313175874613852" euler="-1.5707963267948966 -7.329206686002008e-15 1.9081958235744767e-17">
                                    <joint name="elbow_actuator_elbow_joint" type="hinge" axis="4.2704310576841334e-07 -2.025841991275525e-07 -1.0000004184208011" pos="0.008337119618791935 -0.07313194836712064 -0.008237834961413401" />
                                    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
                                    <inertial mass="0.6203304910388688" pos="0.008406450565535717 -0.12262707524001298 0.010368940685065315" fullinertia="0.0006510003996204108 0.0001662151174014696 0.0005733543537321139 -2.2172555705666176e-05 1.477582968443631e-07 8.20905437074221e-07" />
                                    <body name="wrist_1_actuator" pos="0.006382539328214217 -0.168605908623982 0.01998207046072053" euler="-1.5707963267948966 1.5707963267948963 0">
                                        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
                                        <inertial mass="0.05588569179115005" pos="-0.013154933044560967 -0.009175814107191142 -1.810556621019321e-07" fullinertia="7.5103626001488855e-06 1.2037413533204e-05 1.4109760903696476e-05 -6.650557424940087e-08 -5.27265772856777e-10 4.839065848664722e-10" />
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

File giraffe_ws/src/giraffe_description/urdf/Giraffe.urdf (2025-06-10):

<?xml version='1.0' encoding='utf-8'?>
<robot name="Giraffe">
    <link name="shoulder_pan_shaft">
        <inertial>
            <origin xyz="-1.3411175948422894e-05 -1.3413911005231149e-05 0.0054896999786519405" rpy="-1.9721522630525295e-31 -0.0 -5.3705059693060124e-36" />
            <mass value="0.0042142577056196355" />
            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
        </inertial>
        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
    </link>
    <link name="wrist_2-v9">
        <inertial>
            <origin xyz="0.022107035876708283 -0.0024145862541423745 0.0020810339635840692" rpy="0.0 -1.1035243124313145e-19 8.271806125530277e-25" />
            <mass value="0.16364143755293722" />
            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
        </inertial>
        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
    </link>
    <link name="shoulder_pan">
        <inertial>
            <origin xyz="-0.01822896953375897 0.021931068618284814 -0.0002003754497433663" rpy="0.0 -4.408103815583578e-38 -1.2037062152420224e-35" />
            <mass value="0.3368588301981278" />
            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
        </inertial>
        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
    </link>
    <link name="shoulder_pan_actuator">
        <inertial>
            <origin xyz="-0.01660904534478622 0.010224261326460258 0.015641478472640823" rpy="9.62964972193618e-35 -0.0 0.0" />
            <mass value="0.05588569179115004" />
            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
        </inertial>
        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
    </link>
    <link name="servo_driver_mount">
        <inertial>
            <origin xyz="0.001630541046037175 -0.023904153792526434 -6.560797611575798e-05" rpy="0.0 -0.0 0.0" />
            <mass value="0.08394897351119068" />
            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
        </inertial>
        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
    </link>
    <link name="base_link">
        <inertial>
            <origin xyz="-1.412344777073935e-06 -0.01167323000933829 0.014490543974002491" rpy="0.0 0.0 0.0" />
            <mass value="0.7829139108662936" />
            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
        </inertial>
        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
    </link>
    <link name="clamp_base">
        <inertial>
            <origin xyz="0.032246656601094485 0.00018430716484798106 0.022451728724565186" rpy="0.0 -4.115492114111131e-23 -5.169878828456424e-26" />
            <mass value="0.635930553849011" />
            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
        </inertial>
        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
    </link>
    <link name="retainer">
        <inertial>
            <origin xyz="-0.006296255043728922 2.1136136761608083e-05 0.002929194215944322" rpy="0.0 2.5688772358502946e-32 2.465190328815662e-32" />
            <mass value="0.023167704459451238" />
            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
        </inertial>
        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
    </link>
    <link name="base_brace_right">
        <inertial>
            <origin xyz="2.8448689466038514e-05 0.001644568172768899 -0.009998725532180912" rpy="-9.86076131526265e-32 -0.0 0.0" />
            <mass value="0.0028935307298555263" />
            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
        </inertial>
        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
    </link>
    <link name="base_brace_left">
        <inertial>
            <origin xyz="2.0449101299808704e-05 0.0016310305709314223 0.01000121214225005" rpy="9.86076131526265e-32 -0.0 0.0" />
            <mass value="0.0028935307422124647" />
            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
        </inertial>
        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
    </link>
    <link name="shoulder_lift">
        <inertial>
            <origin xyz="0.0574280722581142 0.0038752636055021483 -0.018696280987126945" rpy="0.0 -1.103508233852567e-19 -8.271806125530277e-25" />
            <mass value="0.48698957738534054" />
            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
        </inertial>
        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
    </link>
    <link name="elbow_link">
        <inertial>
            <origin xyz="-0.04946391966283853 -6.168329873652567e-06 -0.01869059879429968" rpy="4.81482486096809e-35 1.3591653431382697e-37 0.0" />
            <mass value="0.6203304910388688" />
            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
        </inertial>
        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
    </link>
    <link name="wrist1_link">
        <inertial>
            <origin xyz="-0.013205597082802533 -7.378162940874233e-07 -0.01773537593438737" rpy="0.0 1.8807909613156598e-37 0.0" />
            <mass value="0.15229083826066625" />
            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
        </inertial>
        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
    </link>
    <link name="gripper">
        <inertial>
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

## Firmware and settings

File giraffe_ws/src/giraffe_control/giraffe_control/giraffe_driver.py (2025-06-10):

#!/usr/bin/env python3
import rclpy
from rclpy.node import Node
from sensor_msgs.msg import JointState
from giraffe_control.feetech import FeetechMotorsBus
import numpy as np

class GiraffeDriver(Node):

    def __init__(self):
        super().__init__("giraffe_driver")

        self.motors_bus = FeetechMotorsBus(
            port="/dev/ttyACM0",
            motors={
                "shoulder_pan_actuator_shoulder_pan_joint": (1, "sts3215"),
                "shoulder_lift_actuator_shoulder_lift_joint": (2, "sts3215"),
                "elbow_actuator_elbow_joint": (3, "sts3215"),
                "wrist_1_actuator_wrist_1_joint": (4, "sts3215"),
                "wrist_2_actuator_wrist_2_joint": (5, "sts3215"),
                "finger_actuator_gripper_joint": (6, "sts3215"),
            },
        )
        self.motor_order = [
            "shoulder_pan_actuator_shoulder_pan_joint",
            "shoulder_lift_actuator_shoulder_lift_joint",
            "elbow_actuator_elbow_joint",
            "wrist_1_actuator_wrist_1_joint",
            "wrist_2_actuator_wrist_2_joint",
            "finger_actuator_gripper_joint",
        ]
        self.motors_bus.connect()

        self.joint_reverse = {}
        self.offsets = []
        for motor_name in self.motor_order:
            self.declare_parameter(f'joint_reverse.{motor_name}', False)
            joint_reverse_param_value = self.get_parameter(f'joint_reverse.{motor_name}').get_parameter_value().bool_value
            self.joint_reverse[motor_name] = joint_reverse_param_value

            self.declare_parameter(f'joint_offset.{motor_name}', 0.0)
            joint_offset_param_value = self.get_parameter(f'joint_offset.{motor_name}').get_parameter_value().double_value
            self.offsets.append(joint_offset_param_value)

        self.get_logger().info(f'Loaded joint_reverse: {self.joint_reverse}')

        self.joint_state_pub = self.create_publisher(JointState, "/feedback", 10)
        self.joint_command_sub = self.create_subscription(
            JointState, "/command", self.joint_state_callback, 10
        )

        self.timer = self.create_timer(0.01, self.publish_joint_states)

        self.set_motor_acceleration(20, 50)

    def joint_state_callback(self, msg: JointState):
        positions = []

        for motor_name, offset in zip(self.motor_order, self.offsets):
            if motor_name in msg.name:
                idx = msg.name.index(motor_name)
                radians = msg.position[idx]
                if self.joint_reverse[motor_name]:
                    radians = -radians
                model = self.motors_bus.motors[motor_name][1]
                step_value = self.radians_to_steps(-radians, model) + self.radians_to_steps(offset, model)
                positions.append(step_value)
            else:
                positions.append(0)

        self.motors_bus.write("Goal_Position", np.array(positions), self.motor_order)

    def publish_joint_states(self):
        joint_state = JointState()
        joint_state.header.stamp = self.get_clock().now().to_msg()
        joint_state.name = self.motor_order
        positions = self.motors_bus.read("Present_Position", self.motor_order)
        position_radians = self.motors_bus.steps_to_radians(positions, self.motors_bus.motors[self.motor_order[0]][1])

        for motor_name, position, offset in zip(self.motor_order, position_radians, self.offsets):
            radians = -position + offset
            if self.joint_reverse[motor_name]:
                radians = -radians
            joint_state.position.append(radians)

        self.joint_state_pub.publish(joint_state)

    def set_motor_acceleration(self, acceleration: int, gripper_acceleration: int):
        try:
            motor_names = self.motors_bus.motor_names
            non_gripper_motors = motor_names[:-1]
            accelerations = [acceleration] * len(non_gripper_motors)
            self.motors_bus.write("Acceleration", accelerations, non_gripper_motors)
            gripper = motor_names[-1]
            self.motors_bus.write("Acceleration", gripper_acceleration, gripper)
        except Exception as e:
            self.get_logger().warn(f"Failed to set acceleration: {e}")

    def radians_to_steps(self, radians: float, model: str) -> int:
        resolution = 4096
        degrees = np.degrees(radians)
        steps = int(degrees / 360.0 * resolution)
        return steps


def main(args=None):
    rclpy.init(args=args)
    giraffe_driver = GiraffeDriver()

    try:
        rclpy.spin(giraffe_driver)
    except KeyboardInterrupt:
        pass

    giraffe_driver.destroy_node()
    giraffe_driver.motors_bus.disconnect()
    rclpy.try_shutdown()


if __name__ == '__main__':
    main()

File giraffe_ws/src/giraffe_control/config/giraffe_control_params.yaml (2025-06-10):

giraffe_driver:
  ros__parameters:
    joint_reverse.shoulder_pan_actuator_shoulder_pan_joint: true
    joint_reverse.shoulder_lift_actuator_shoulder_lift_joint: false
    joint_reverse.elbow_actuator_elbow_joint: true
    joint_reverse.wrist_1_actuator_wrist_1_joint: true
    joint_reverse.wrist_2_actuator_wrist_2_joint: true
    joint_reverse.finger_actuator_gripper_joint: false

    joint_offset.shoulder_pan_actuator_shoulder_pan_joint: 3.223
    joint_offset.shoulder_lift_actuator_shoulder_lift_joint: 4.6138
    joint_offset.elbow_actuator_elbow_joint: 1.4083
    joint_offset.wrist_1_actuator_wrist_1_joint: 3.152
    joint_offset.wrist_2_actuator_wrist_2_joint: 1.5708
    joint_offset.finger_actuator_gripper_joint: 4.9532

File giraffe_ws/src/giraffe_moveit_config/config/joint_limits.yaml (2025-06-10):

# @format

# joint_limits.yaml allows the dynamics properties specified in the URDF to be overwritten or augmented as needed

# For beginners, we downscale velocity and acceleration limits.
# You can always specify higher scaling factors (<= 1.0) in your motion requests.  # Increase the values below to 1.0 to always move at maximum speed.
default_velocity_scaling_factor: 1.0
default_acceleration_scaling_factor: 1.0

# Specific joint properties can be changed with the keys [max_position, min_position, max_velocity, max_acceleration]
# Joint limits can be turned off with [has_velocity_limits, has_acceleration_limits]
joint_limits:
  shoulder_pan_actuator_shoulder_pan_joint:
    has_velocity_limits: true
    max_velocity: 1.0
    has_acceleration_limits: true
    max_acceleration: 1.0
  wrist_1_actuator_wrist_1_joint:
    has_velocity_limits: true
    max_velocity: 1.0
    has_acceleration_limits: true
    max_acceleration: 1.0
  elbow_actuator_elbow_joint:
    has_velocity_limits: true
    max_velocity: 1.0
    has_acceleration_limits: true
    max_acceleration: 1.0
  shoulder_lift_actuator_shoulder_lift_joint:
    has_velocity_limits: true
    max_velocity: 1.0
    has_acceleration_limits: true
    max_acceleration: 1.0
  wrist_2_actuator_wrist_2_joint:
    has_velocity_limits: true
    max_velocity: 1.0
    has_acceleration_limits: true
    max_acceleration: 1.0
  finger_actuator_gripper_joint:
    has_velocity_limits: true
    max_velocity: 1.0
    has_acceleration_limits: true
    max_acceleration: 1.0

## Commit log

2025-06-09 updated with new cad files for v1.1
    [Giraffe Leader v1.1.stl, Giraffe v1.1.f3d, Giraffe v1.1.step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]
2025-06-10 updated moveit pkg
    [Giraffe.urdf, base_brace_left.stl, base_brace_right.stl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]
2025-06-10 moveit sim funct with v1.1
    [giraffe.ros2_control.xacro, giraffe.xacro.urdf]
2025-06-10 moveit_integration functional
    [giraffe_hardware.xacro.urdf]
2025-06-11 updated assets and cad
    [Giraffe v1.1.f3d, as5600_servo_1.f3d, as5600_servo_1.step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]
2025-06-11 bom updated
2025-06-11 updated BOM heading
2025-06-11 updated BOM
2025-06-11 material fixedgazebo material fix
    [giraffe.urdf.xacro, giraffe.xacro.urdf, giraffe_hardware.xacro.urdf]
2025-06-12 pcb and announcement added
2025-06-13 updated cad and assets
    [as5600_servo_2.f3d, as5600_servo_2.step, as5600_servo_2.stl]
2025-06-13 updated assembly docs link
2025-06-14 leader calib bug fix for mac
    [as5600_reader.py, leader_calibration.py]
